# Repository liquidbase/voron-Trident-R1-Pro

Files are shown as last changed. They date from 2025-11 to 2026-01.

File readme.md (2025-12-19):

# voron Trident R1 Pro

Buildlog of voron Trident R1 Pro from start to finish with all modifications and finally INDX from Bondtech.

Where possible, corresponding build videos are also included in the readme. When what was done and which files were used will be noted in any case.

# Videolog

# Buildlog

- 2025-12-15 Rebuild Toolhead
- 2025-12-14 Rebuild EBay
- 2025-12-07 Added Backpanel
- 2025-12-06 Part 3 of EBay (Cables)
- 2025-12-05 Part 2 of EBay (M8P & PSU)
- 2025-12-04 Part 1 of EBay (Layout)
- 2025-12-03 Build beltpath and carriage
- 2025-12-02 Build fanblocks for skirts
- 2025-11-30 Bedmount
- 2025-11-30 XY-Assembly
- 2025-11-30 Z-Assembly
- 2025-11-30 Frontidler
- 2025-11-30 A/B Drives
- 2025-11-28 Framebuild mostly done

# Configlog

- 2025-12-16 Finished Config
- 2025-12-16 Added print_start
- 2025-12-15 Finished config (motors, heater, bed mesh)
- 2025-12-15 Cartographer installed
- 2025-12-15 Added config for A, B, Z0, Z1, Z2-Motor, thermistor
- 2025-12-15 added canbus-uuid for toolhead
- 2025-12-12 Added config to git
- 2025-12-12 klipper-screen installed
- 2025-12-12 klipper-backup installed
- 2025-12-12 KIAUH installed
- 2025-12-06 Preparing SDCard with MainsailOS

# Filelog

- 2025-12-16 Update misc_assembly
- 2025-12-16 Added umbilical plate
- 2025-12-15 Added printfiles for cartographer
- 2025-12-15 Added image of uuid for docs
- 2025-12-15 Added pinout for EBB36
- 2025-12-15 Added thermistor mount
- 2025-12-15 Update misc_assembly
- 2025-12-15 Added printfiles for cable tie mount and front usb connector
- 2025-12-12 Update printfiles
- 2025-11-28 Added printfile for corner bracket
- 2025-11-28 Added printfiles for Dragon Burner Carriage with Cartographer Mount
- 2025-11-28 Added printfiles for Dragon Burner
- 2025-11-28 Update shopping list
- 2025-11-28 Added doc for Manta M8P v2
- 2025-11-28 Added docs for Trident (Formbot)
- 2025-11-28 Update 3mf
- 2025-11-23 Added shopping list
- 2025-11-23 Added first 3mf
- 2025-11-23 Added print files
- 2025-11-23 Added readme.md

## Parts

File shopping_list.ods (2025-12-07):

Voron Trident R1 Pro |  |  |  |  | Gesamt: | 1,003.93 €
lfd Nr. | Part | Einzelpreis | Menge | Preis | Status
1 | VORON Trident R1 Pro CoreXY 3D Printer Kit (https://www.formbot3d.com/products/voron-trident-r1-pro-corexy-3d-printer-kit-with-best-quality-parts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) | 660.46 € | 1 | 660.46 €
2 | Extrudr DuraPro PA12-CF (https://extrudr.com/de/de/products/durapro-pa12-cf/) | 111.74 € | 1 | 111.74 €
3 | Extrudr DuraPro ASA GF rot (https://extrudr.com/de/de/products/durapro-asa-gf/?variant=UHJvZHVjdFZhcmlhbnQ6NDExNg%3D%3D) | 45.29 € | 1 | 45.29 €
4 | Bondtech OEM Set für Sherpa Mini RIDGA V2 (https://www.3djake.de/bondtech/oem-set-fuer-sherpa-mini-ridga-v2?sai=17363) | 47.78 € | 1 | 47.78 €
5 | Cartographer (https://meltbro.de/product_info.php?no_boost=1) | 50.98 € | 1 | 50.98 €
6 | EBB36 v2 (https://www.amazon.de/BIGTREETECH-Erweiterungsgerät-Kommunikation-STM32G0B1CBT6-Mehrfachsicherheitsschutz/dp/B0B1LC5YS2/) | 28.78 € | 1 | 28.78 €
7 | CM4 (https://www.berrybase.de/raspberry-pi-compute-module-4/ram-4gb/flash-ohne-lite-/wlan-bluetooth-ja) | 58.90 € | 1 | 58.90 €
8 | Extrudr DuraPro PC/PBT-CF (https://extrudr.com/de/de/products/durapro-pc-pbt-cf/) | 35.69 € | 2 | 71.38 €

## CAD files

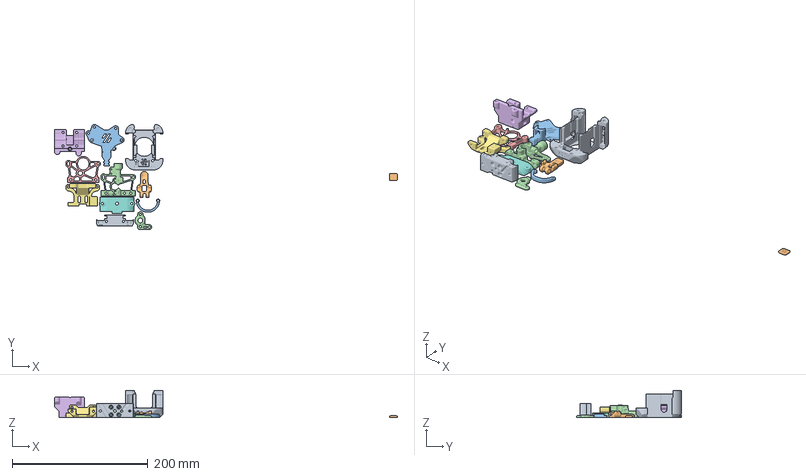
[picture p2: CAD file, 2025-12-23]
printfiles/06_toolhead_assembly.3mf
506.0 x 155.4 x 40.0 mm
Cowl_NoProbe.stl
[c]_Voron_Diffuser.stl
EBB_G2SA.stl
housing_core_std^housing_sherpa_mini_a3_r16(FDM)(FilamentSensor)(ECAS04)
housing_rear_x1_rev17.STL
mgn12h_x_carriage_g2sa.stl
cartograph-mount_long.stl
Sherpa_Mini_Mount.stl
Dragon_Mount.stl
[a]_idler_arm_long_x1_rev16a.STL
Brace_Loop.stl
[a]_housing_front_x1_rev15.STL

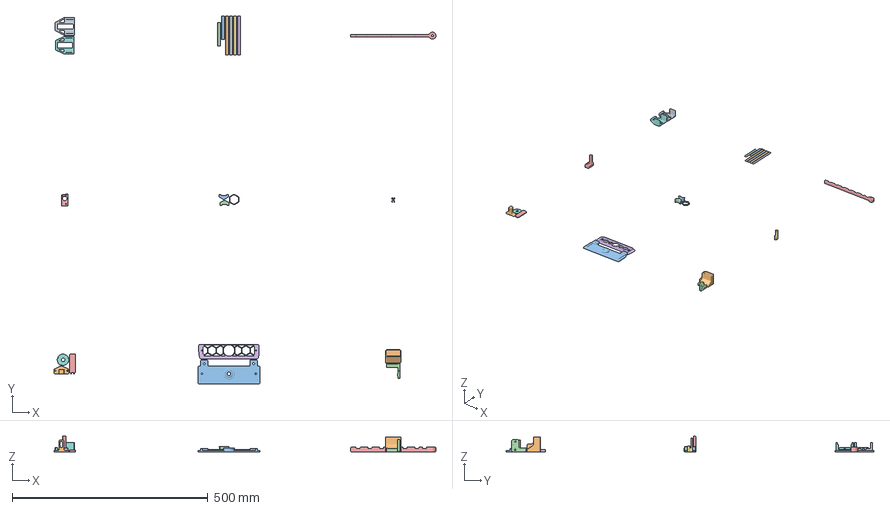
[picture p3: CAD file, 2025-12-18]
printfiles/08_misc_assembly.3mf
977.0 x 940.6 x 40.0 mm
ulc3_fan_mount_side_fan_support.stl
bucket.stl
Cover.stl
brush-holder.stl
carto_nozzle_offset_tool.step_3
Grill.stl
Thermistor_Mount_2020_5mm.stl
carto_nozzle_offset_tool.step_2
lock v1
carto_nozzle_offset_tool.step_1
PG7 Gantry Adapter.stl
slot_cover_one_side.stl x 6
wago_221_413_fan_mount_side_fan_support.stl
swing_arm.stl

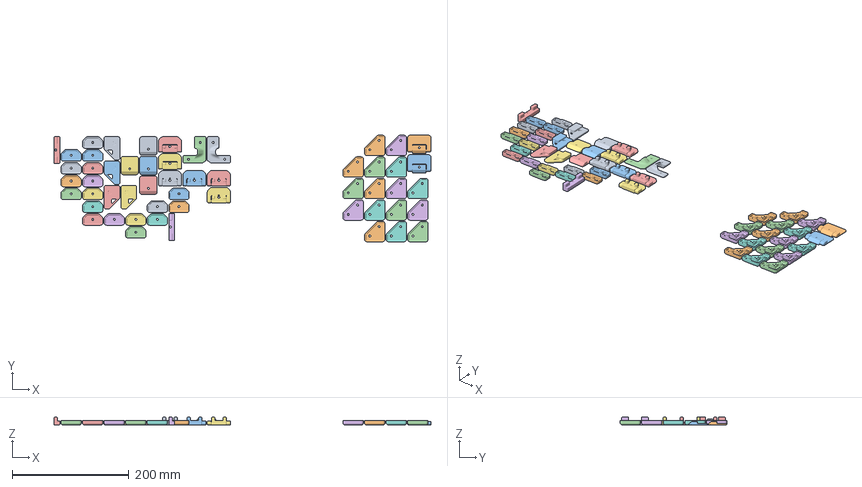
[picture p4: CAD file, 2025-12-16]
printfiles/07_panel_assembly.3mf
647.0 x 183.0 x 13.0 mm
wire_cover_left.stl
bottom_panel_hinge_x2.stl x 2
wire_cover_right.stl
door_hinge_x6.stl x 6
corner_panel_clip_4mm_x8.stl x 16
bottom_panel_clip_x4.stl x 4
handle_a_x2.stl x 2
handle_b_x2.stl x 2
midspan_panel_clip_4mm_x7.stl x 18
latch_x2.stl x 2

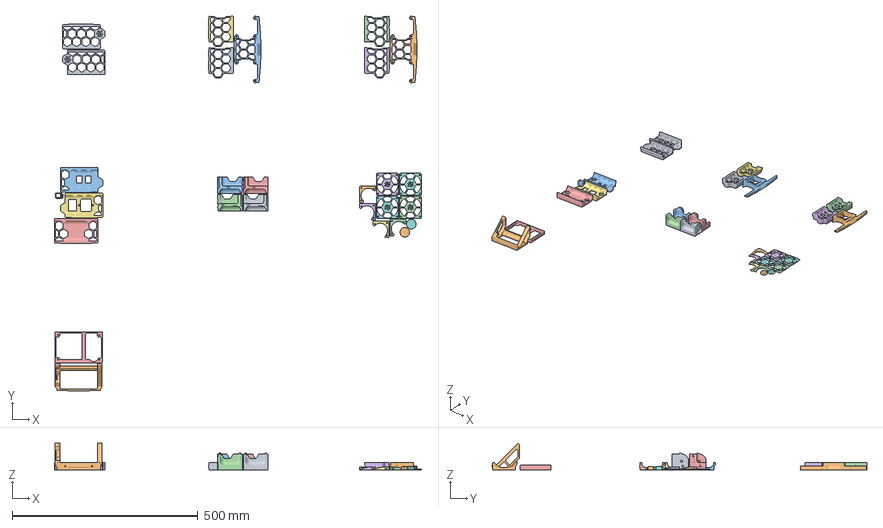
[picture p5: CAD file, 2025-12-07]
printfiles/04_skirt_assembly_250.3mf
988.7 x 1009.6 x 72.4 mm
front_skirt_a_250.stl
side_fan_support_x2.stl x 2
side_skirt_b_250_x2.stl x 2
BTT HDMI5 V1_2 mount frame_Regular.stl
side_skirt_a_250_x2.stl x 2
[a]_fan_grill_b_x2.stl x 2
BTT HDMI5 V1_2 mount bracket_Regular.stl
keystone_panel.stl
corner_a_x2.stl x 2
[a]_fan_grill_a_x2.stl x 2
power_inlet_filtered.stl
front_skirt_b_250.stl
[a]_corner_baseplate_b_x2.stl x 2
[a]_keystone_blank_insert_x2.stl
rear_center_skirt_250.stl
[a]_corner_baseplate_a_x2.stl x 2
[a]_skirt_logo_x2.stl x 2
corner_b_x2.stl x 2

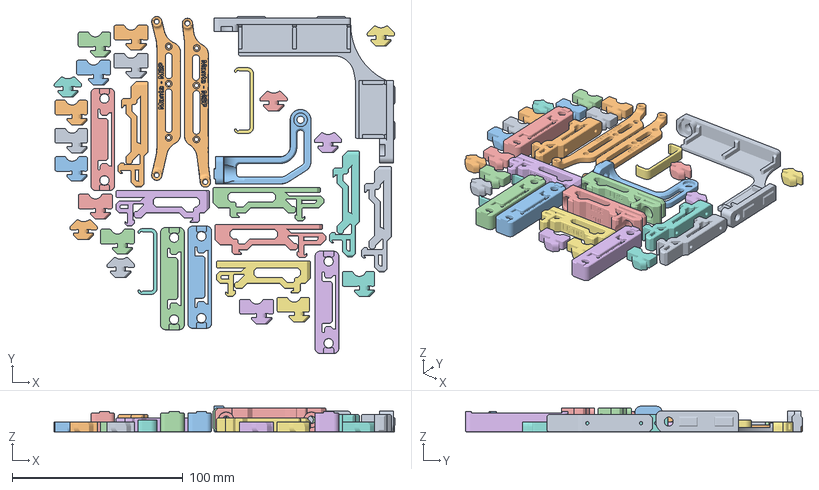
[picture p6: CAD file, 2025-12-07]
printfiles/05_ebay_assembly.3mf
199.6 x 197.6 x 15.0 mm
wago_221-415_corner_mount.stl
manta-8p-din.stl
PSU_stabilizer_50mm.stl
lrs_psu_bracket_x2.stl x 2
UHP_200_Mount_x2.stl x 2
pcb_din_clip_x3.stl x 3
DIN_frame_mount_x4.stl x 4
DIN_center_support_x2.stl x 2
deck_support_3mm_optional_x6.stl x 6
deck_support_4mm_optional_x6.stl x 6
cable_frame_anchor_x6.stl x 6

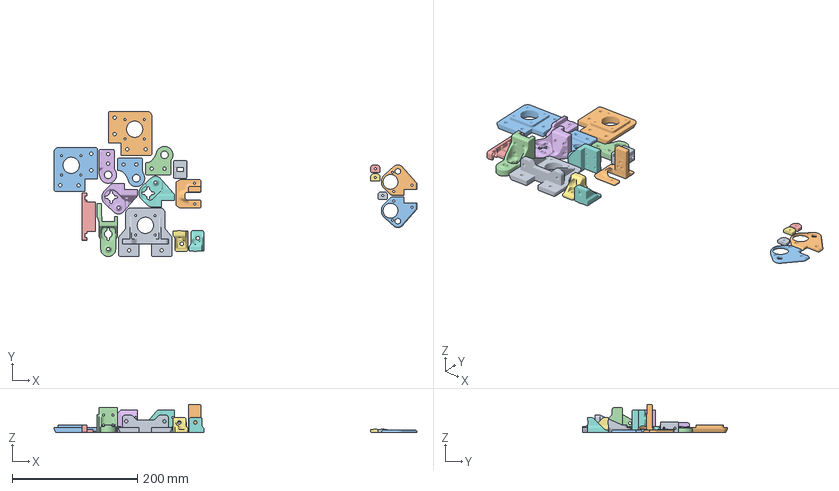
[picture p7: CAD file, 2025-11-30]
printfiles/03_Z_assembly.3mf
579.9 x 231.8 x 45.0 mm
z_stepper_rear.stl
[a]_z_carriage_left.stl
[a]_z_carriage_right.stl
z_carriage_rear_3hole.stl
[a]_z_rail_stop_x3.stl x 3
z_carriage_left.stl
z_carriage_right.stl
z_cable_chain_mount_3hole.stl
z_bed_left.stl
z_bed_right.stl
wago_221-412_mount.stl
z_bed_rear.stl
z_rear_extrusionbracket_right.stl
z_rear_extrusionbracket_left.stl
nozzle_probe.stl
z_stepper_right.stl
z_stepper_left.stl

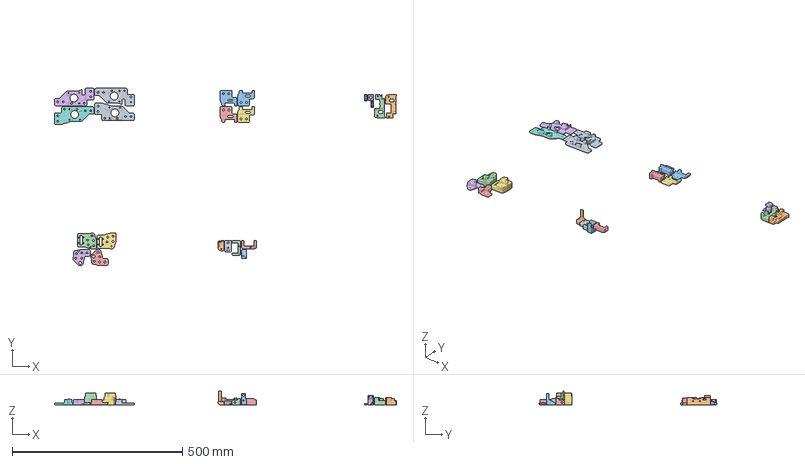
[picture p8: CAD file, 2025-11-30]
printfiles/02_gantry_assembly.3mf
1004.4 x 521.4 x 40.0 mm
a_drive_frame_lower.stl
x_frame_V2TR_MGN12_left.stl
front_idler_b_x2.stl x 2
x_frame_V2TR_MGN12_right.stl
[a]_tensioner_left.stl
pinda_adapter.stl
probe_retainer_bracket.stl
b_drive_frame_upper.stl
probe_retainer_bracket_9mm.stl
front_idler_a_x2.stl x 2
[a]_tensioner_right.stl
a_drive_frame_upper.stl
xy_joint_left_lower_MGN12.stl
b_drive_frame_lower.stl
[a]_y_endstop_housing.stl
[a]_wire_cover.stl
[a]_y_endstop_bumper.stl
xy_joint_right_lower_MGN12.stl
xy_joint_left_upper_MGN12.stl
xy_joint_right_upper_MGN12.stl

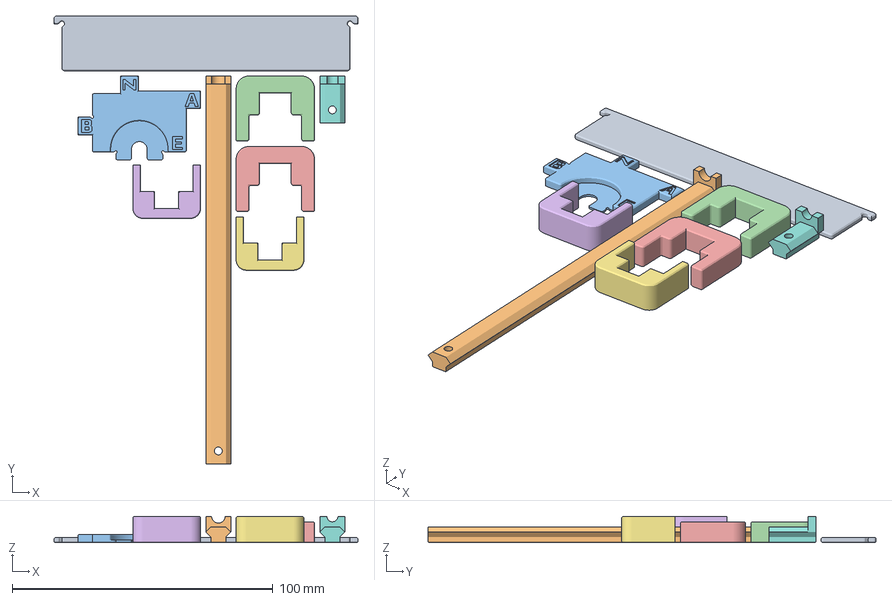
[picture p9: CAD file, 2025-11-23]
printfiles/01_tools_assembly.3mf
116.5 x 171.8 x 10.1 mm
110mm_Y_alignment_spacer_x2.stl
140mm_extrusion_drill_guide.stl
pulley_jig.stl
MGN12_rail_guide_x2.stl x 2
MGN9_rail_guide_x2.stl x 2
10mm_extrusion_drill_guide.stl

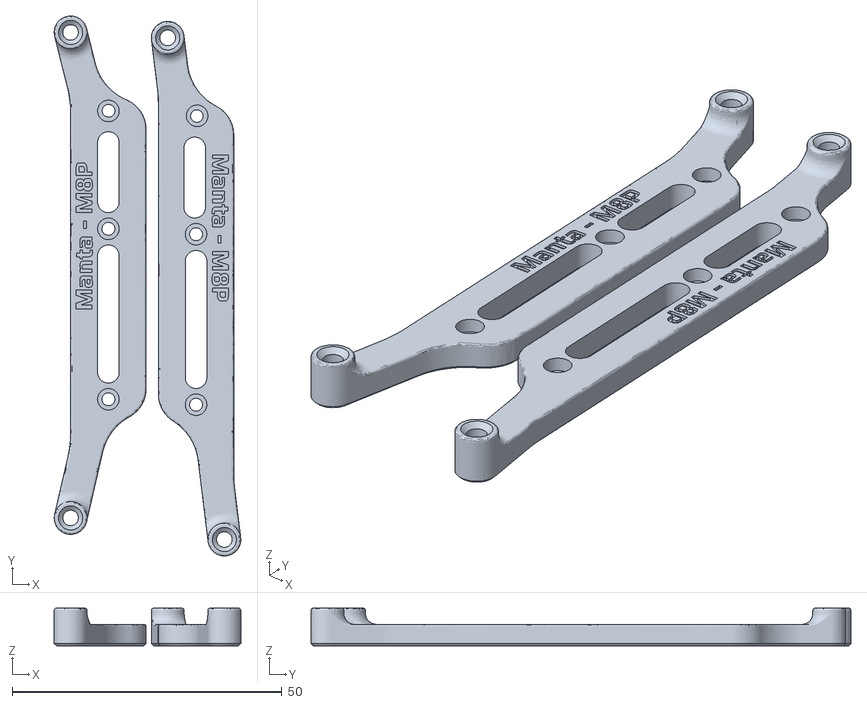
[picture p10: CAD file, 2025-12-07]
printfiles/ElectronicsBay/Controller_Mounts/manta-8p-din.stl
34.6 x 100.1 x 7.00

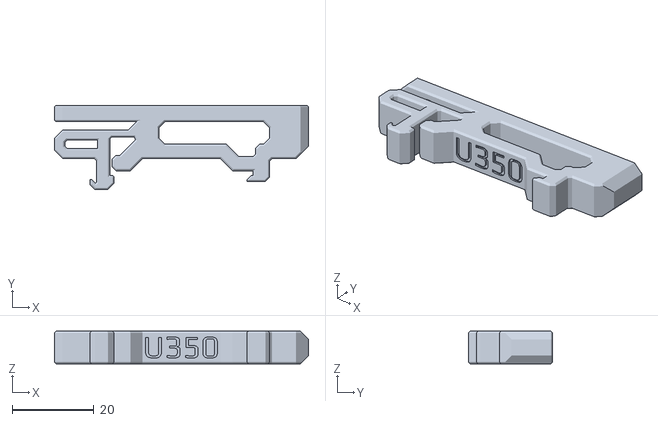
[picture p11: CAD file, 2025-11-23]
printfiles/ElectronicsBay/Other_PS_Mounts/UHP_350_Mount_x2.stl
62.0 x 20.6 x 8.00

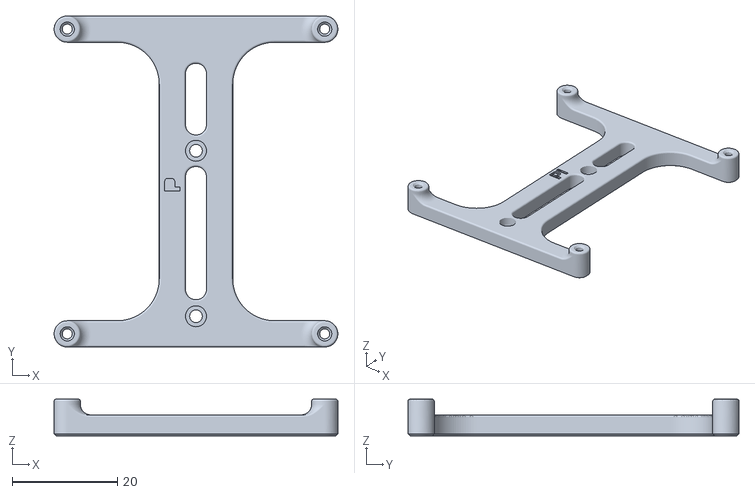
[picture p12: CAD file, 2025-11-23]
printfiles/ElectronicsBay/raspberrypi_bracket.stl
54.0 x 63.0 x 7.00

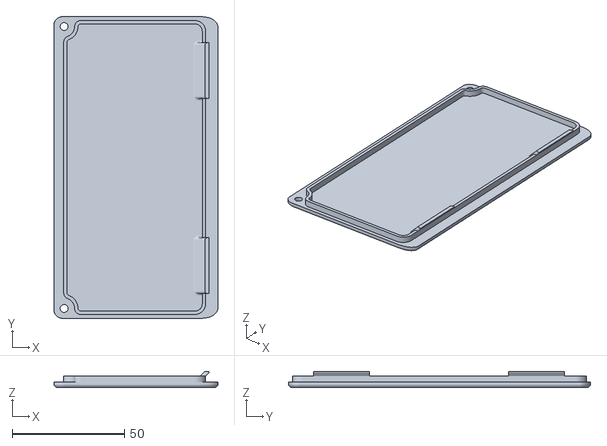
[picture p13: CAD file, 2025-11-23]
printfiles/Exhaust_Filter/[a]_filter_access_cover.stl
73.2 x 134.8 x 7.20

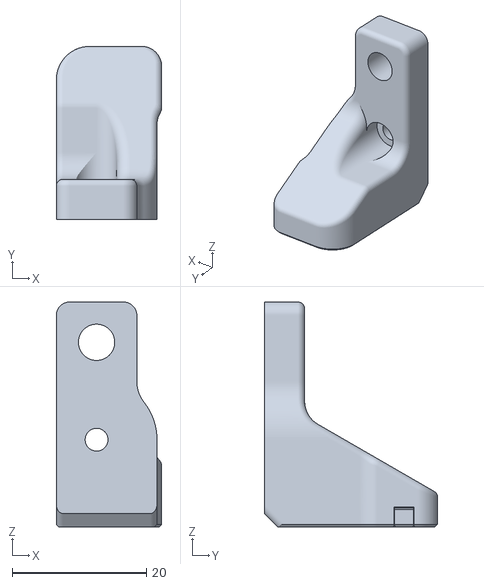
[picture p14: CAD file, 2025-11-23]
printfiles/Gantry/AB_Drive_Units/[a]_y_endstop_bumper.stl
15.7 x 25.8 x 33.5

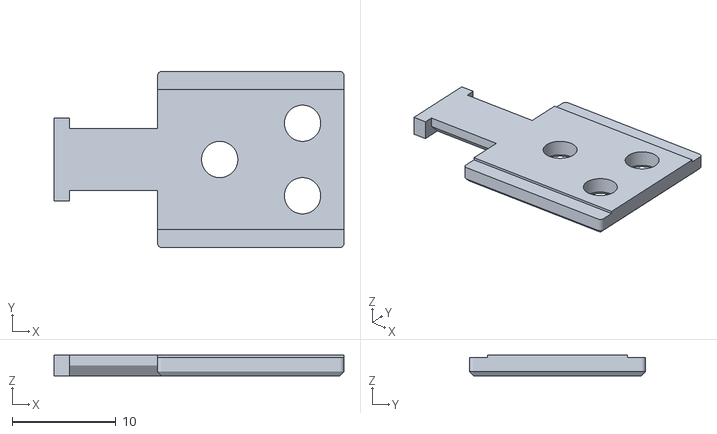
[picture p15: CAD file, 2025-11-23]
printfiles/Gantry/chain_wire_anchor_3hole_x2.stl
28.0 x 17.0 x 2.00

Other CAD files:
printfiles/Gantry/Front_Idlers/[a]_tensioner_right.stl
printfiles/Gantry/X_Axis/X_Carriage/probe_retainer_bracket.stl
printfiles/Gantry/X_Axis/XY_Joints/[a]_endstop_pod_D2F_switch.stl
printfiles/Misc/6mm slot cover by filotto78/STL/slot_cover.stl
printfiles/ElectronicsBay/Controller_Mounts/BIGDIPPER_bracket_set.stl
printfiles/ElectronicsBay/Controller_Mounts/BTT_MOT_EXP_bracket.stl
printfiles/ElectronicsBay/Controller_Mounts/Duet2_Duet3Mini5_bracket_set.stl
printfiles/ElectronicsBay/Controller_Mounts/GTR_bracket_set.stl
printfiles/ElectronicsBay/Controller_Mounts/Octopus_bracket_set.stl
printfiles/ElectronicsBay/Controller_Mounts/S6_bracket_set.stl
printfiles/ElectronicsBay/Controller_Mounts/SKR_Pro_bracket_set.stl
printfiles/ElectronicsBay/Controller_Mounts/SKR_bracket_inline_set.stl
printfiles/ElectronicsBay/Controller_Mounts/Spider_bracket_set.stl
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

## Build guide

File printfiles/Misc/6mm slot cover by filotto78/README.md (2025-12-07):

# Cover for extrusion with 6mm slot width

Two simple files.
One is symmetric and can be used for slots that are inside the printer.
One isn't symmetric and can be used on external frames, where there are clear panels.

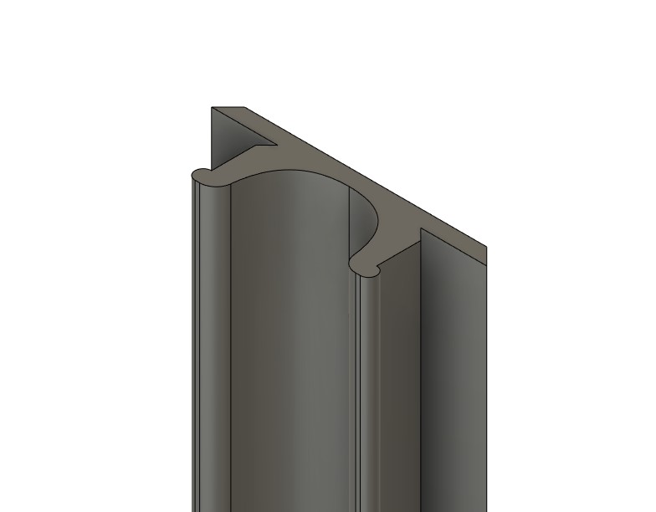
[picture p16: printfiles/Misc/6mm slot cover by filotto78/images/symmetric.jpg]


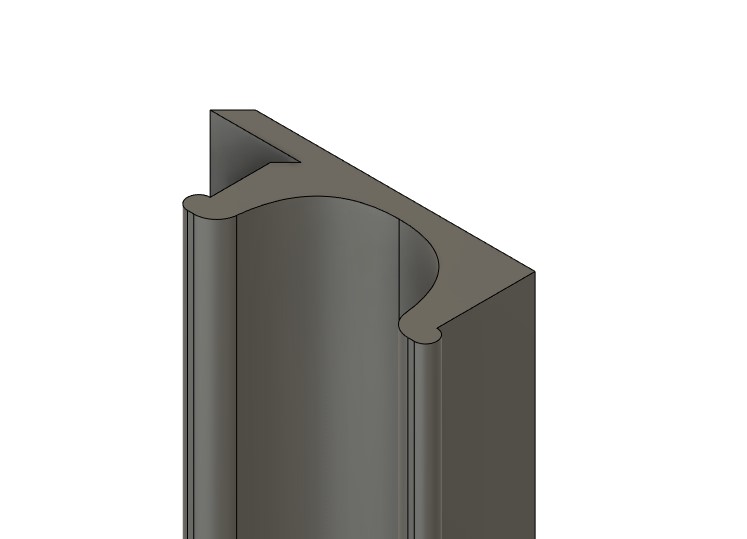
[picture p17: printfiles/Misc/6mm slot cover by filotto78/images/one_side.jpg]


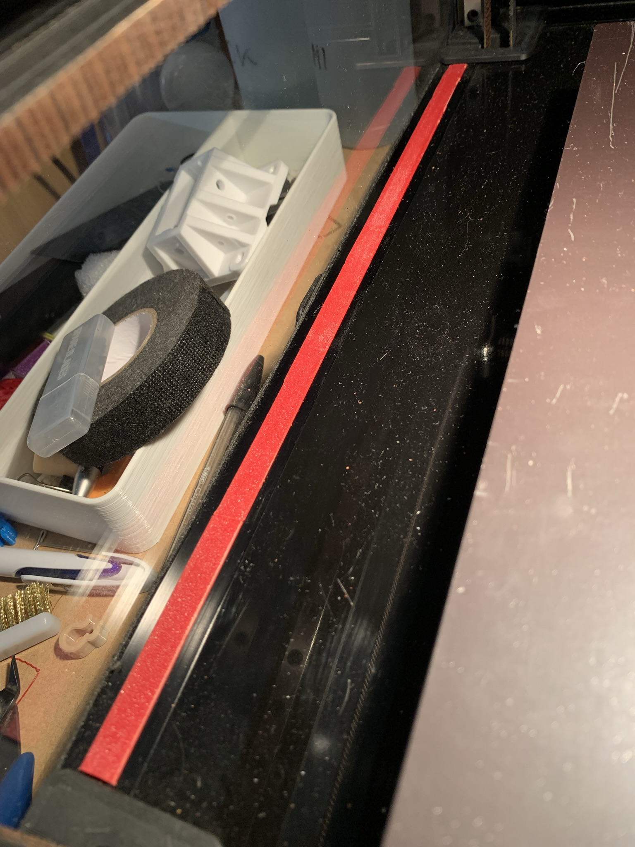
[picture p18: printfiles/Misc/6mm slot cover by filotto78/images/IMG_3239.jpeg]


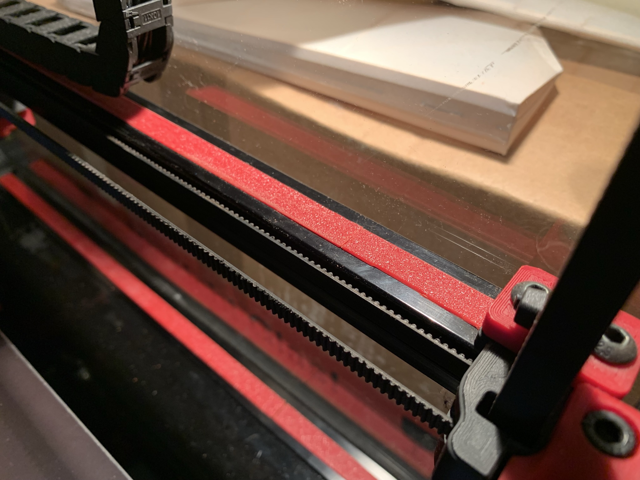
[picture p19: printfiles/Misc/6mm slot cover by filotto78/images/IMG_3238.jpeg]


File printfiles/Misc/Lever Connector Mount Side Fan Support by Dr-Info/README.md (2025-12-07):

# Lever Connector Mount using Side Fan Supports (V2.4 & VT)

This allows you to mount Universal Lever Connectors or WAGO 221 using the side fan supports.
This mod will only fit the following push connectors:
  * WAGO 221-413 or 221-415
  * [Universal Lever Connector](https://a.co/d/4dFjRUR) (Length x Width x Height)
      * 3 port - 18 x 18.6 x 10
      * 5 port - 18 x 29.8 x 10

### Printing
  * Print 1 mount per set of skirt fans
  * Default Voron settings
  * No supports needed

### BOM
Item | Size | Qty | Comment 
--- | --- | --- | ---
Lever Connector | 3 or 5 port | 2 | per mount
BHCS | M5x16 | 1 | per mount

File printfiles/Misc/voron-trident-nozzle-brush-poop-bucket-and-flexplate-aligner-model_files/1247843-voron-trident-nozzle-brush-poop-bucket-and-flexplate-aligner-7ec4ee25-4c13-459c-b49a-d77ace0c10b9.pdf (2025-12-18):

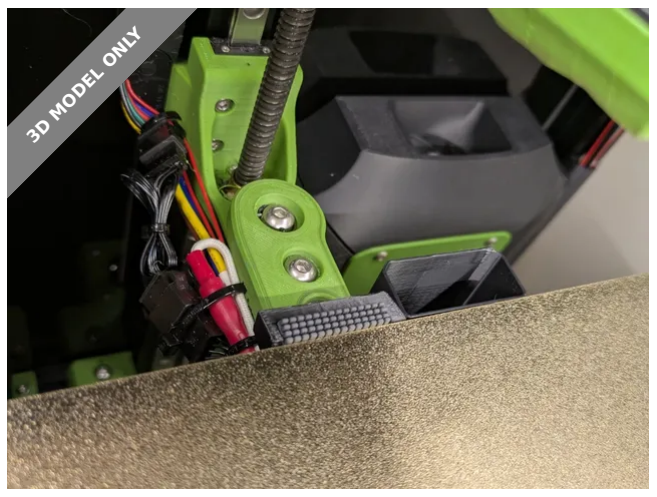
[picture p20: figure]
3D MODEL ONLY

## Summary

All in one piece, poop bucket is attached with magnets to make it easy to empty.

3D Printers (https://printables.com/model?categoryId=1) > Voron Parts & Upgrades (https://printables.com/model?categoryId=137)

Tags: | magnet | brush | plateholder | voron | brushholder
flexplate | poopbucket

All in one solution for nozzle brush, flex plate stop/alignment and poop bucket.
I designed it primarily for use with TAP where the nozzle is barely able to reach brushes since TAP pushes the nozzle forward. So i positioned the brush right on the edge of the bed.

Check the Z distance between the top of your bed and the top of the brush holder. I included both step and Fusion file if you want to change the height if its too high/low. You want it to be just high enough so the flexplate hits it. If it sticks up too much you might run into problem if your scanner hits it.
BOM:

1x Bambu mini clone silicone brush. Available on aliexpress, amazon...

E (https://printables.com/@EEE_1665175) EEE (https://printables.com/@EEE_1665175)

## Voron Trident Nozzle brush, poop bucket and flexplate aligner

VIEW IN BROWSER (https://printables.com/model/1247843-voron-trident-nozzle-brush-poop-bucket-and-flexpla)

updated 29. 3. 2025 | published 29. 3. 2025

## Model files

6x 6x3mm neodynium magnets

2x M3 T-nuts/Hammerhead nuts

2x M3x8mm BHCS screw to attach it to the
Installation instructions:
Flame and/or clean the brush area before attaching the brush to make it stick better.
Glue the magnets in place with some super glue

## License

This work is licensed under a
Creative Commons (4.0 International License)

Attribution (http://creativecommons.org/licenses/by/4.0/)

✖ | Sharing without ATTRIBUTION
✔ | Remix Culture allowed
✔ | Commercial Use

brush-holder.stl

trident-nozzle-scrubber.f3d

bucket.stl

trident-nozzle-scrubber.step

✔ | Free Cultural Works
✔ | Meets Open Definition

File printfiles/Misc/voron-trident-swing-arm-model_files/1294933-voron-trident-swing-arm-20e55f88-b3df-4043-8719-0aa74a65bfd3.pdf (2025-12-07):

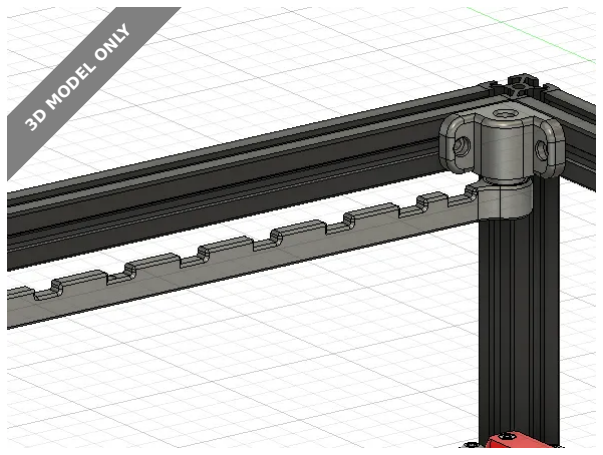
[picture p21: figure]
3D MODEL ONLY

## Summary

Extrusion mountable swing-arm for Voron or other printers using extrusions

3D Printers (https://printables.com/model?categoryId=1) > Voron Parts & Upgrades (https://printables.com/model?categoryId=137)

Tags: | swing | voron | swingarm | trident300

For my Voron Trident 300 I want to get rid of the cable-chains and go for umbilical. Unfortunatly umbilical never worked out for me, as I wanted. I used a Tophat for my Trident, but was not happy with it (hard to seal, more air to heat, ...). With the swing-arm there is no more need for a Tophat.

Luckily I found the swing-arm from Prusa and I remixed it to be useable on a Trident. The base and the arm are fully printable (use supports).

For the assembly you need the following hardware:

2x F695-2RS Bearings (5 mm x 13 mm x 4 mm)
1x M5 Heatset-Insert (~9mm long)
1x M5x30
2x M3 Hammerhead/Rollin

On my assembly, the two bearings have friction - therefore you maybe can't fully tighten the screw and leave it a bit loose. Use some Loctite to not unscrew.

z (https://printables.com/@zeke_544128) zeke- (https://printables.com/@zeke_544128)

## Voron Trident Swing Arm

VIEW IN BROWSER (https://printables.com/model/1294933-voron-trident-swing-arm)

updated 22. 5. 2025 | published 22. 5. 2025

•
•
•
•

## Model files

There is also a hole in the front of the arm, to use piano-wire and a hole for a heatset to lock the wire (not tested, because it works for me without the wire).

Important:

Please note, that you have to feed the PTFE-tube for your filament from the side (I drilled a whole in the side-panel).

Printed with Polymaker ASA, bearings have a good fit on my assembly.

At the moment I'm working on new version with smaller bearings and a second arm to prevent sagging of the arm. This version is fully working, at least for me.

Update:

22.05.2025: Added Step-File (had to redraw completly..)

## This remix is based on

Prusa SwingArm - Open-Source release (https://printables.com/model/1168002-prusa-swingarm-open-source-release) by Prusa Research (https://printables.com/@Prusa3D)

base.stl

swing_arm.stl

swing_arm.f3d

## License

This work is licensed under a GNU

Lesser General Public License (https://www.gnu.org/licenses/lgpl-3.0.html)

✖ | Sharing without ATTRIBUTION
✔ | Remix Culture allowed
✔ | Commercial Use
✔ | Meets Open Definition

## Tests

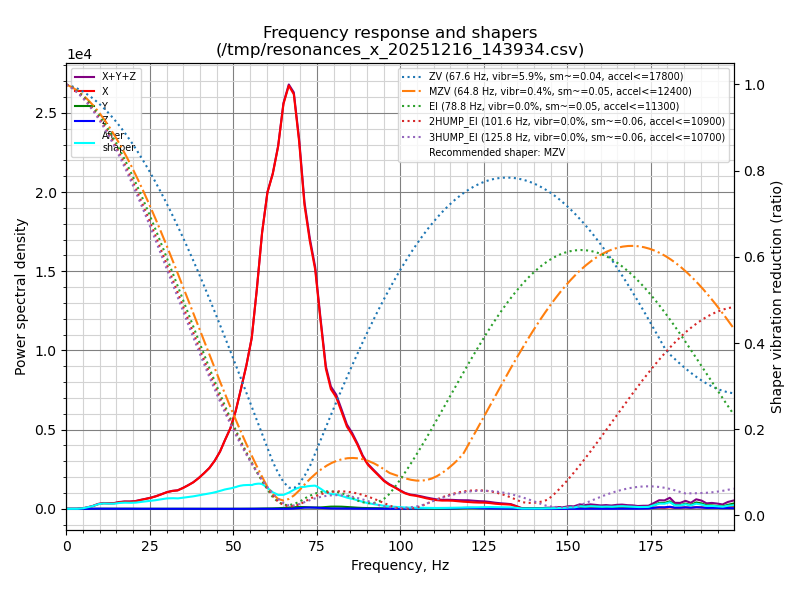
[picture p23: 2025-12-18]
config/ShakeTune_results/input_shaper/shaper_calibrate_x.png

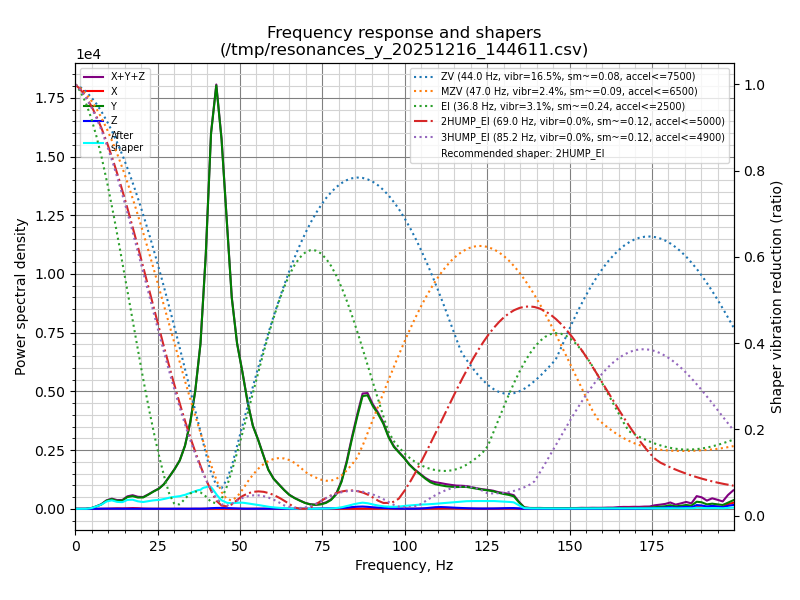
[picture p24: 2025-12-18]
config/ShakeTune_results/input_shaper/shaper_calibrate_y.png

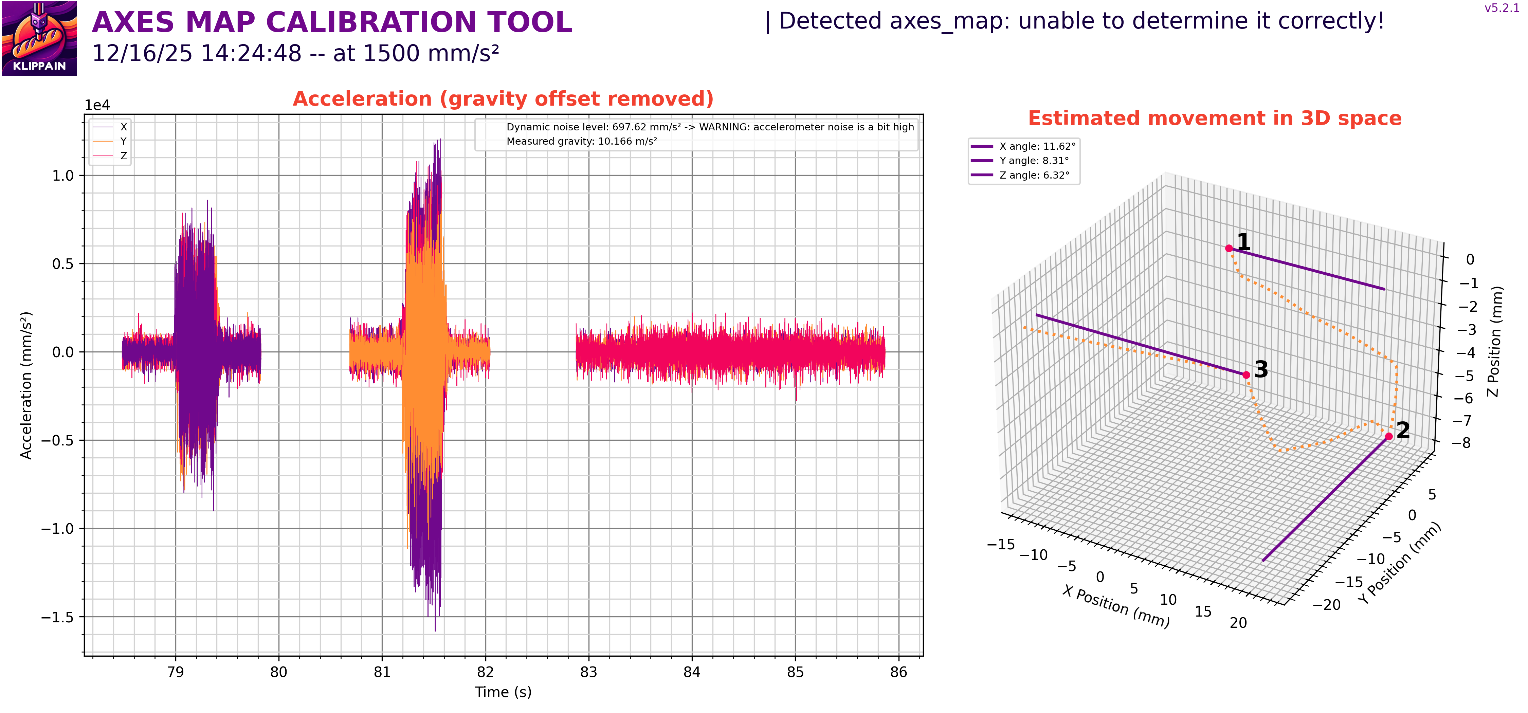
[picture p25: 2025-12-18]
config/ShakeTune_results/axes_map/axesmap_20251216_142448.png

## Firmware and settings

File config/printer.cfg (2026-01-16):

# includes
[include mainsail.cfg]
[include hardware/ebb36.cfg]
[include hardware/cartographer.cfg]
[include hardware/fans.cfg]
[include macros/macros.cfg]
[include led-effect/effects.cfg]

# main config
[mcu]
canbus_uuid: f052a554d892

[printer]
kinematics: corexy
max_velocity: 300  
max_accel: 10000
max_z_velocity: 15
max_z_accel: 350
square_corner_velocity: 5.0

# thermistors
# chamber
[thermistor NTC10K]
temperature1: 0.0
resistance1: 32116.0
temperature2: 40.0
resistance2: 5309.0
temperature3: 80.0
resistance3: 1228.0

# sensors
[temperature_sensor MCU]
sensor_type: temperature_mcu

[temperature_sensor SoC]
sensor_type: temperature_host

[temperature_sensor chamber]
sensor_type: NTC10K
sensor_pin: PB0
min_temp: 0
max_temp: 100

# stepper
# x-stepper (B-Motor)
[stepper_x]
step_pin: PE6
dir_pin: PE5
enable_pin: !PC14
microsteps: 32
rotation_distance: 40
full_steps_per_rotation:200
endstop_pin: tmc2209_stepper_x:virtual_endstop
position_min: 0
position_endstop: 252
position_max: 252
homing_speed: 50
homing_retract_dist: 0
homing_positive_dir: true

[tmc2209 stepper_x]
uart_pin: PC13
interpolate: True
run_current: 0.8
sense_resistor: 0.110
stealthchop_threshold: 0
diag_pin: ^PF4
driver_SGTHRS: 95

# y-stepper (A-Motor)
[stepper_y]
step_pin: PE2
dir_pin: PE1
enable_pin: !PE4
microsteps: 32
rotation_distance: 40
endstop_pin: tmc2209_stepper_y:virtual_endstop
full_steps_per_rotation:200
position_min: 0
position_endstop: 260
position_max: 260
homing_speed: 50
homing_retract_dist: 0
homing_positive_dir: true

[tmc2209 stepper_y]
uart_pin: PE3
interpolate: True
run_current: 0.8
sense_resistor: 0.110
stealthchop_threshold: 0
diag_pin: ^PF3
driver_SGTHRS: 95

## Z0 Stepper - Front Left on MOTOR3_A
[stepper_z]
step_pin: PB8
dir_pin: PB7
enable_pin: !PE0
rotation_distance: 4
microsteps: 32
endstop_pin: probe:z_virtual_endstop
position_max: 250
position_min: -2.5
homing_speed: 8.0
second_homing_speed: 3
homing_retract_dist: 0

[tmc2209 stepper_z]
uart_pin: PB9
interpolate: true
run_current: 0.6
sense_resistor: 0.110
stealthchop_threshold: 0

##	Z1 Stepper - Rear  on Motor5
[stepper_z1]
step_pin: PB4
dir_pin: PB3
enable_pin: !PB6
rotation_distance: 4
microsteps: 32

[tmc2209 stepper_z1]
uart_pin: PB5
interpolate: true
run_current: 0.6
sense_resistor: 0.110
stealthchop_threshold: 0

##	Z2 Stepper - Front Right on Motor6
[stepper_z2]
step_pin: PG13
dir_pin: PG12
enable_pin: !PG15
rotation_distance: 4
microsteps: 32

[tmc2209 stepper_z2]
uart_pin: PG14
interpolate: true
run_current: 0.6
sense_resistor: 0.110
stealthchop_threshold: 0

# bed heater
[heater_bed]
##	SSR Pin - HE1
heater_pin: PA0
sensor_type: Generic 3950
sensor_pin: PB1
max_power: 1
min_temp: 0
max_temp: 125
#control: pid
#pid_kp: 58.437
#pid_ki: 2.347
#pid_kd: 363.769

# LED Control
[output_pin caselight_left]
pin: PA3
pwm: true
shutdown_value: 0
value: 0.1
cycle_time: 0.01

[output_pin caselight_right]
pin: PA1
pwm: true
shutdown_value: 0
value: 0.1
cycle_time: 0.01

[neopixel statusbar]
pin: PD15
chain_count: 18
color_order: GRB
initial_RED: 1.0
initial_GREEN: 1.0
initial_BLUE: 1.0

# Homing and Gantry Adjustment Routines
[idle_timeout]
timeout: 1800

[safe_z_home]
home_xy_position: 125,125
speed: 100
z_hop: 10

[z_tilt]
z_positions:
    -50, 18
    125, 298
    300, 18
points:
    30, 5
    125, 195
    220, 5

# Bed Mesh
[bed_mesh]
speed: 600
horizontal_move_z: 5
mesh_min: 25, 32
mesh_max: 225, 225
probe_count: 50, 50
    
# additional pinouts
[board_pins]
aliases:
    # EXP1 header
    EXP1_1=PE7, EXP1_2=PG1,
    EXP1_3=PG0, EXP1_4=PF15,
    EXP1_5=PF14, EXP1_6=PF13,    # Slot in the socket on this side
    EXP1_7=PF12, EXP1_8=PF11,
    EXP1_9=<GND>, EXP1_10=<5V>,
    
    # EXP2 header
    EXP2_1=PE13, EXP2_2=PE12,
    EXP2_3=PE15, EXP2_4=PE11,
    EXP2_5=PE10, EXP2_6=PE14,      # Slot in the socket on this side
    EXP2_7=PE8, EXP2_8=<RST>,
    EXP2_9=<GND>, EXP2_10=<NC>
    
# Exclude print objects & Firmware Retraction & Skew Correction
[exclude_object]

[firmware_retraction]

[skew_correction]

# Input Shaper
[input_shaper]
shaper_freq_x: 64.8
shaper_type_x: mzv
shaper_freq_y: 69
shaper_type_y: 2hump_ei

[shaketune]
result_folder: ~/printer_data/config/ShakeTune_results
number_of_results_to_keep: 10
keep_raw_data: False
show_macros_in_webui: True
timeout: 600
measurements_chunk_size: 2
max_freq: 200
dpi: 300

#*# <---------------------- SAVE_CONFIG ---------------------->
#*# DO NOT EDIT THIS BLOCK OR BELOW. The contents are auto-generated.
#*#
#*# [heater_bed]
#*# control = pid
#*# pid_kp = 62.832
#*# pid_ki = 3.406
#*# pid_kd = 289.814
#*#
#*# [skew_correction CaliFlower]
#*# xy_skew = -0.0005038654055135586
#*# xz_skew = 0.0
#*# yz_skew = 0.0
#*#
#*# [cartographer scan_model default]
#*# coefficients = 1.4933866324303149,1.9536336664116143,0.8302571244431369,0.41219385753590077,0.38846083000287757,0.3662982079837586,-0.17118549999057256,-0.2553043229468969,0.2582270328446492,0.22432767649948993
#*# domain = 3.204578716162053e-07,3.3287676213511595e-07
#*# z_offset = 0
#*# reference_temperature = 23.65
#*# software_version = 1.3.3
#*# mcu_version = CARTOGRAPHER 5.0.0
#*#
#*# [cartographer touch_model default]
#*# threshold = 858
#*# speed = 2
#*# z_offset = -0.05
#*# software_version = 1.3.3
#*# mcu_version = CARTOGRAPHER 5.0.0

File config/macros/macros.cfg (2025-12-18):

[gcode_macro PRINT_START]
gcode:
  {% set target_bed = params.BED|int %}
  {% set target_extruder = params.EXTRUDER|int %}
  {% set x_wait = printer.toolhead.axis_maximum.x|float / 2 %}
  {% set y_wait = printer.toolhead.axis_maximum.y|float / 2 %}

  G28
  G90
  BED_MESH_CLEAR

  {% if params.BED|int > 90 %}
    SET_DISPLAY_TEXT MSG="Bed: {target_bed}c"
    M106 S255

    G1 X{x_wait} Y{y_wait} Z15 F9000
    M190 S{target_bed}

  {% else %}
    SET_DISPLAY_TEXT MSG="Bed: {target_bed}c"
    G1 X{x_wait} Y{y_wait} Z15 F9000
    M190 S{target_bed}
    SET_DISPLAY_TEXT MSG="Soak for 5 min"
    G4 P300000
  {% endif %}

  SET_DISPLAY_TEXT MSG="Hotend: 150c"
  M109 S150

  SET_DISPLAY_TEXT MSG="Leveling"
  Z_TILT_ADJUST
  G28 Z
  SET_DISPLAY_TEXT MSG="Bed mesh"
  BED_MESH_CALIBRATE
  CARTOGRAPHER_TOUCH_HOME

  SET_DISPLAY_TEXT MSG="Hotend: {target_extruder}c"
  G1 X{x_wait} Y{y_wait} Z15 F9000
  M107
  M109 S{target_extruder}

  SET_DISPLAY_TEXT MSG="Printer goes brr"
  G0 X{x_wait - 50} Y4 F10000
  G0 Z0.4
  G91
  G1 X100 E20 F1000
  G90
  SKEW_PROFILE LOAD=CaliFlower

[gcode_macro PRINT_END]
gcode:
    # safe anti-stringing move coords
    {% set th = printer.toolhead %}
    {% set x_safe = th.position.x + 20 * (1 if th.axis_maximum.x - th.position.x > 20 else -1) %}
    {% set y_safe = th.position.y + 20 * (1 if th.axis_maximum.y - th.position.y > 20 else -1) %}
    {% set z_safe = [th.position.z + 2, th.axis_maximum.z]|min %}
    
    SET_SKEW CLEAR=1
    SAVE_GCODE_STATE NAME=STATE_PRINT_END
   
    M400
    G92 E0
    G1 E-25 F1800
    
    TURN_OFF_HEATERS
    
    G90
    G0 X125 Y225 Z{z_safe} F20000
    G0 X{th.axis_maximum.x//2} Y{th.axis_maximum.y - 15} F3600
    M107
    
    BED_MESH_CLEAR
    RESTORE_GCODE_STATE NAME=STATE_PRINT_END
    # Stop fans
    SET_FAN_SPEED FAN=controller_right SPEED=0
    SET_FAN_SPEED FAN=controller_left SPEED=0
    #SET_PIN PIN=caselight_left VALUE=0.1
    #SET_PIN PIN=caselight_right VALUE=0.1
  
[gcode_macro LOAD_FILAMENT]
variable_ignore_min_extrude_temp: True
gcode:
  M117 Loading
  M104 S240
  G90
  G1 X100 Y20 Z20 F1800
  M104 S240
  TEMPERATURE_WAIT SENSOR={printer.toolhead.extruder} MINIMUM=240
  M83
  G1 E50 F300
  G1 E50 F300
  G1 E-4 F1800
  M82
  M400
  M104 S0
  M117 Loading done

[gcode_macro UNLOAD_FILAMENT]
variable_ignore_min_extrude_temp: True
gcode:
  M117 Unloading
  M104 S240
  TEMPERATURE_WAIT SENSOR={printer.toolhead.extruder} MINIMUM=240
  M83
  G1 E5 F500
  G1 E-50 F1000
  G1 E-50 F1000
  M82
  M400
  TURN_OFF_HEATERS
  M117 Unloading done

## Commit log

2025-11-23 correct printer in title
2025-11-23 Add assembly manual
2025-11-23 Added shopping list
    [shopping_list.ods]
2025-11-23 Added 3mf files
    [01_tools_assembly.3mf, 03_Z_assembly.3mf, 04_skirt_assembly_250.3mf]
2025-11-25 Update Shopping List
    [shopping_list.ods]
2025-11-26 Update 3mf for assembly
2025-11-28 Update 3MF
    [04_skirt_assembly_250.3mf]
2025-11-30 Added last 3mf
    [05_ebay_assembly.3mf, 06_toolhead_assembly.3mf, 07_panel_assembly.3mf]
2025-11-30 Added STL for Toolhead
    [Brace_Loop.stl, Cowl_NoProbe.stl, Dragon_Mount.stl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]
2025-12-07 Added misc printfiles for Mods
    [08_misc_assembly.3mf, 2020_cover_one_side.f3d, 2020_cover_simmetric.f3d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]
2025-12-12 Update print file
    [07_panel_assembly.3mf]
2025-12-12 Added first config
    [ebb36.cfg, mainsail.cfg, printer.cfg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]
2025-12-15 Added printfiles for cable tie mount and front usb connector
    [cable_tie_mount.stl, skirt-usb-no-markings.step, usb-skirt-insert-1-no-marking.stl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]
2025-12-15 Update misc assembly
    [08_misc_assembly.3mf]
2025-12-15 Added thermistor mount
    [Thermistor_Mount_2020_5mm.stl]
2025-12-15 Update misc_assembly
    [08_misc_assembly.3mf]
2025-12-15 CANBus-IDs for Manta & EBB
2025-12-15 Update misc:assembly
    [08_misc_assembly.3mf]
2025-12-15 Added printfiles for cartographer and update misc_assembly
    [08_misc_assembly.3mf, carto_nozzle_offset_tool.3mf, carto_nozzle_offset_tool.step]
2025-12-16 Added umbilical plate
    [Cover.stl, Grill.stl]
2025-12-18 Update config
    [08_misc_assembly.3mf, brush-holder.stl, bucket.stl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]
2025-12-18 Fix Carto Touch home, remove adaptive mesh
    [macros.cfg]
2025-12-18 Removed doubled command
    [macros.cfg]
2025-12-23 Update toolhead assembly & files
    [06_toolhead_assembly.3mf, EBB_G2SA.f3d, EBB_G2SA.step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]
2026-01-16 current config
    [printer.cfg]
